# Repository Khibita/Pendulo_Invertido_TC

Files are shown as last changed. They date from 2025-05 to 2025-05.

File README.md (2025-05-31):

# 🧩 Proyecto: Péndulo Invertido

## 📋 Introducción
Este proyecto se centra en diseñar, construir y poner en marcha un péndulo invertido. Este es un sistema muy conocido en ingeniería de control porque es un ejemplo clásico de un sistema que no es lineal, es inestable y además tiene doble integración. 

El péndulo invertido presenta un desafío interesante, ya que hay que crear un sistema de control capaz de mantenerlo en equilibrio vertical desde cualquier posición inicial y frente a perturbaciones externas. Para lograrlo, se ha implementado un controlador PID usando un microcontrolador ESP32, apoyado por sensores de orientación como acelerómetro y giroscopio, y un sistema de actuadores con motores DC. 

Durante el desarrollo del proyecto, se han trabajado distintas áreas como:
- [ ] el diseño y fabricación del sistema mecánico con impresión 3D.
- [ ] la selección e integración de componentes electrónicos.
- [ ] la programación del controlador en el entorno Arduino y la sintonización del PID para validar el comportamiento del sistema.

Al final, se ha logrado crear un robot que puede mantenerse en posición vertical, resistir pequeñas perturbaciones y desplazarse controladamente. Todo el proceso está bien documentado y puedes consultarlo y reutilizarlo en este repositorio.

---

## 🎯 Objetivos
- [ ] Estabilidad en posición vertical (±5°)
- [ ] Compensación de empujones
- [ ] Arranque desde cualquier posición
- [ ] Implementación en ESP32
- [ ] Sintonización del PID

---

## 🛠️ Hardware
**Componentes usados:**
- [ ] ESP32: [WROOM 32D], elegimos está por su bajo costé, conexiones inalambricas y poder ejecutar codigo c.
- [ ] Sensor: [MPU9250], elegimos está por su bajo costé, y devolver aceleración en 9 ejes.
- [ ] Driver de motor: [TB6612FNG] se ajustaba a las caracteristicas necesarias
- [ ] Motores: [fz3176] Motor de corriente continua que se ajustaba al precio y potencia de consumo
- [ ] Batería: [ MN1604] Coloquialemente conocida de "petaca", produce 9V de alimentación, El sistema necesita más , conexión por cable, para siguie
- [ ] Regulador de Tensión: [LM7805]
- [ ] Condensador: [0.1uF y 0.2uf]
- [ ] Conectores entrada y salida :  3 de 2 pines.

-Recordar que tanto la conexión electrica , como la pcb se adjunta en este mismo repositorio.

---

## 🧱 Diseño mecánico
**Software de diseño usado:**  
- [ ] Para está pieza de geometría simple, pero que contaba con multiples caras, elegí freecad, debido que es con el estoy familiarizado por otras asignaturas y por tener entornos bien organizados y una comunidad activa. Aunque si es tu primera vez realizando este tipo de objetos con varias caras, te recomiendo aplicaciones con interfaces más modernas.

**Método de fabricación:**  
- [ ] Impresora 3D, en concreto la Anet A8. La impresión tardará bastante por culpa de los soportes, para reducir el tiempo, se podría probar o a inclinar la figura o rotar la figura para que el eje y quede como el eje x, precauición  son sujerencias no validadas. 

**Versiones del chasis y decisiones de diseño:**  
- [ ] Solo hay una versión, la publicada, en la cual prioricé que el centro de masas fuera lo más bajo posible y que estuviera centrado, apare de que no fuera necesario, tornillos más que para la placa base, aunque por como está  encastrada, no sería necesaría pasa su funcionamiento, recomiendo encarecidamente pornerlos.Para buscar un balance entre centro de masas bajo y porcentaje de ángulo de giro libre de las ruedas , sin que el chasis toque suelo, hice una incisio (diminuir el espesor a 1) en la parte baja del chasis un rectangulo para colocar la bateria , en caso de usar un portapilas más grande o una batería que superé las dimensiones de la usada habría que modificar el chasis.

---

## 🔌 Montaje
El montaje se divide en 2 partes:
- [ ] Soldar: soldar todos los componentes a la placa, en caso de querer reutilizar los componentes, recomiendo soldar conectores macho hembra a la placa en vez de los propios componentes. IMPORTANTE SEGUIR LAS DIRECCIONES DE LA PCB .
- [ ] Colocar las piezas: recomiendo empezar por la pcb una vez atornillada, seguir con los motores y por último pegar la batería con silicona al hueco posterior a la placa. 
---

## 📈 Control y software
**Controlador:** PID

**Implementación:**  
El lenguaje es .ino, compatible con  Esp32, pero las libreria en las que se basa, los pids a utilizar, está escrita en c++.

**Valores de cte del PID (Op 1 - reajustes pequeños en valores cercanos al (0,0), pero resistente a golpes fuertes):**  
- [ ] Kp = 50.0
- [ ] Ki = 1.0
- [ ] Kd = 20.0

**Valores de cte del PID (Op 1 - se mantiene quieto totalmente, pero sensible a golpes fuertes):**  
- [ ] Kp = 50.0
- [ ] Ki = 2.0
- [ ] Kd = 20.0

**PID Seleccionado**
- [ ] PID Filtrado, opción 3.

De forma resumida el codigo  compara el setpoint (posición destino) y la actual, a través del pid seleccionado, devuelve valores para los motores, que luego de ser normalizador , para enviar a los motores.

---

🎮 Control Inalambrico:

implementé la conexión por Bluetooth para que el sistema pudiera recibir órdenes en tiempo real desde un celular o una app, en mi caso serial terminal bluetooth, como si fuera un control remoto. Lo que hago es leer dos valores que llegan separados por una coma: uno controla el movimiento hacia adelante o atrás, y el otro el giro. Con esos datos, ajusto el setpoint del controlador PID para que el sistema se mueva según lo que el usuario indique, y también modifico la señal de los motores para que pueda girar fácilmente. Además, hice que el sistema mande de vuelta los valores recibidos por Bluetooth, así se puede ver desde el celular que la señal llegó bien y todo está funcionando como se espera.

---

## Resultados
**Hay que distingir dos casos según los valores de Kp, Ki, Kd elegidos:**
- [ ] Op 1:  El sistema llega conseguir estabilizarse en la mayoría de casos a golpes que incluso hagan tocar el suelo con el chasis. Una vez estabilizado empieza a tener pequeños sobre ajustes que hace que oscile un poco.
- [ ] Op 2:  El sistema consigue estabilizarse con golpes pequeños, pero en el caso de que el chasis toque suelo, no será capaz de conseguir levantarse de nuevo hasta chocar con algún objeto. Una vez estabilizado se mantiene estatico.

En resumen dependiendo de la respuestá deseada se puede elegir una u otra e incluso otras convinaciones de Kp, Ki y Kd. 

**Problemas con la Potencia**
- [ ] la conexión bluetooth hace que pierde algo de potencia los motores, por lo que es más sensible a perturbaciones, esto es debido a que el sistema no está pensado para una batería tan sencilla.
- [ ] Problemas de potencia, al romperseme los dos portapilas con que contaba tuve que hacer un arreglo con una batería de 9v auxiliar, por lo que se necesita conectar el robot a una fuente de energía. 

---

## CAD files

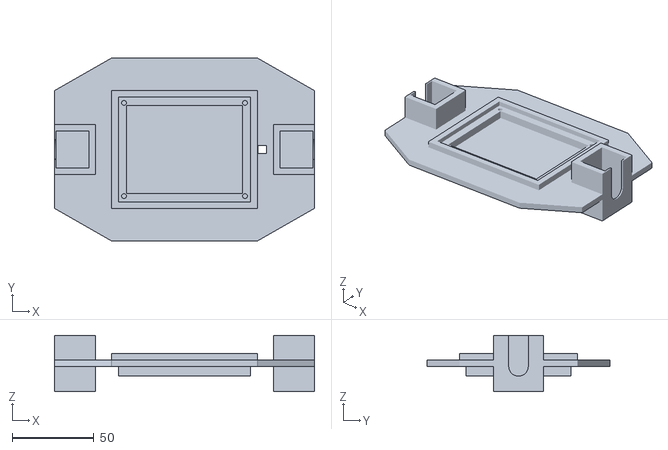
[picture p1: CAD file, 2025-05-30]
Chassis3D.stl
159.0 x 112.0 x 34.5

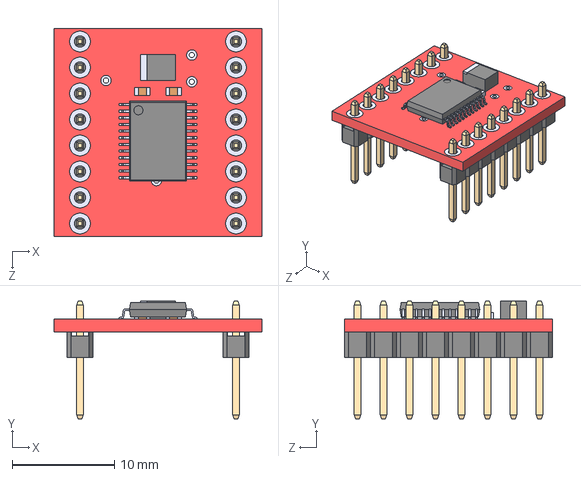
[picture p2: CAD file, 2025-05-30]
pcb-2/ROB-14450 (1)/ROB-14450.step
20.3 x 11.5 x 20.3 mm

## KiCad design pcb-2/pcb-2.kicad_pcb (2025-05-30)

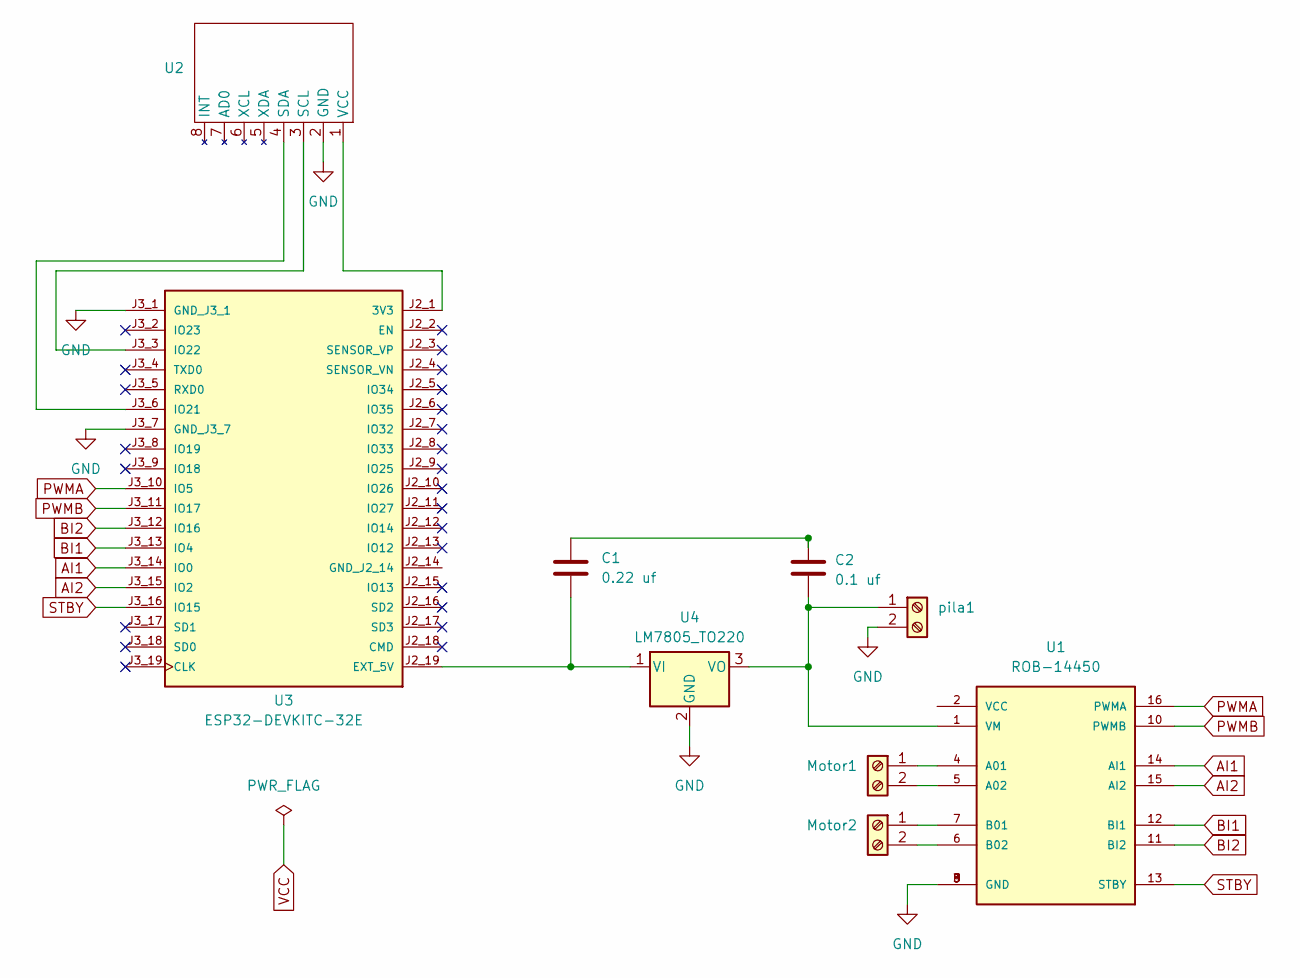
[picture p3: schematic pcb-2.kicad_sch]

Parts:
C1: 0.22 uf; CP_Radial_D5.0mm_P2.00mm
C2: 0.1 uf; CP_Radial_D5.0mm_P2.00mm
Motor1, Motor2: TerminalBlock_Phoenix_MKDS-1,5-2-5.08_1x02_P5.08mm_Horizont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
U1: ROB-14450; MODULE_ROB-14450; PARTREV 11-13-17
U2: MPU-6050
U3: ESP32-DEVKITC-32E; MODULE_ESP32-DEVKITC-32E; PARTREV 1.4
U4: LM7805_TO220; TO-220-3_Vertical
pila1: TerminalBlock_Phoenix_MKDS-1,5-2-5.08_1x02_P5.08mm_Horizont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

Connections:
AI1: U1.14 (AI1), U3.J3_14 (IO0)
AI2: U1.15 (AI2), U3.J3_15 (IO2)
BI1: U1.12 (BI1), U3.J3_13 (IO4)
BI2: U1.11 (BI2), U3.J3_12 (IO16)
GND: U1.3 (GND), U1.8 (GND), U1.9 (GND), U2.2 (GND), U3.J3_1 (GND_J3_1), U3.J3_7 (GND_J3_7), U4.2 (GND), pila1.2
unnamed: C1.1, C2.1
unnamed: Motor1.1, U1.4 (A01)
unnamed: Motor1.2, U1.5 (A02)
unnamed: Motor2.1, U1.7 (B01)
unnamed: Motor2.2, U1.6 (B02)
unnamed: C2.2, U1.1 (VM), U4.3 (VO), pila1.1
unnamed: U2.3 (SCL), U3.J3_3 (IO22)
unnamed: U2.4 (SDA), U3.J3_6 (IO21)
unnamed: U2.1 (VCC), U3.J2_1 (3V3)
unnamed: C1.2, U3.J2_19 (EXT_5V), U4.1 (VI)
PWMA: U1.16 (PWMA), U3.J3_10 (IO5)
PWMB: U1.10 (PWMB), U3.J3_11 (IO17)
STBY: U1.13 (STBY), U3.J3_16 (IO15)

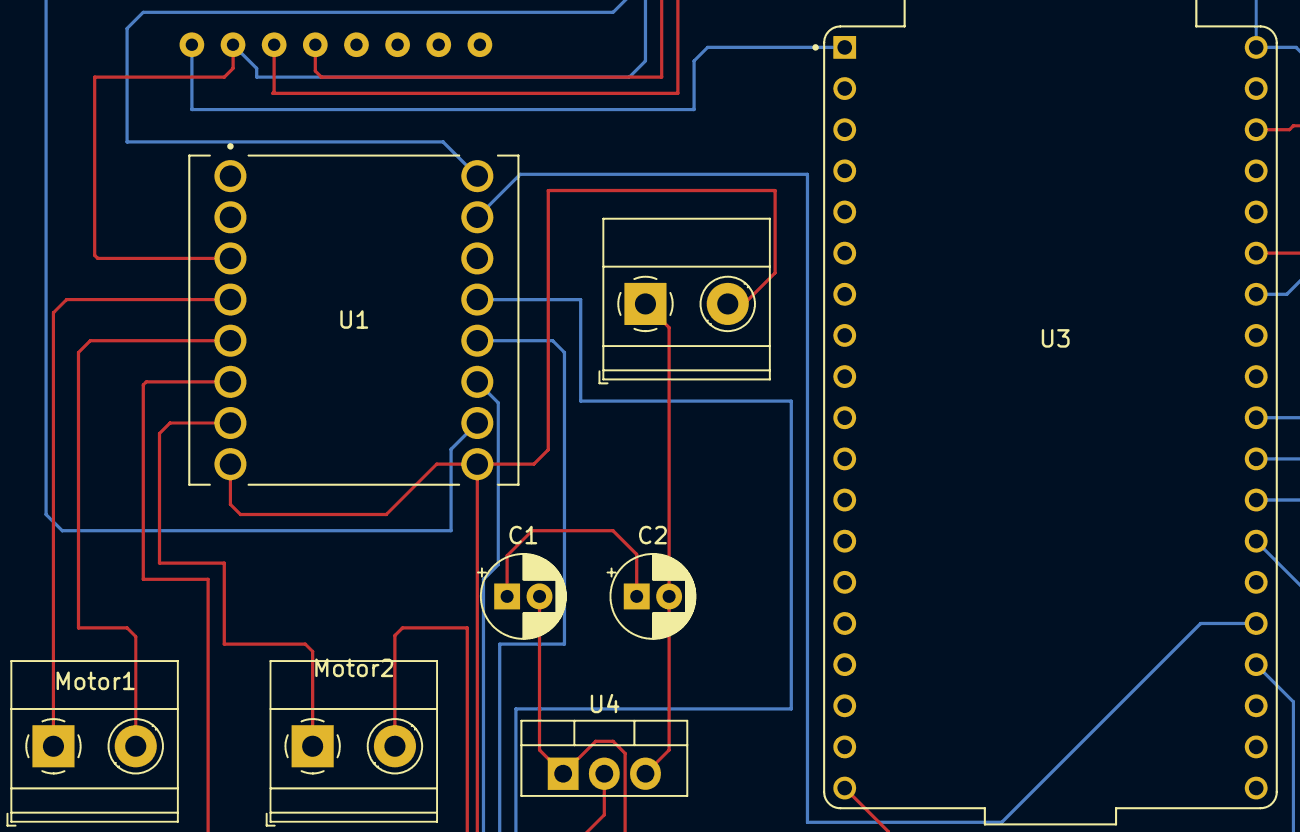
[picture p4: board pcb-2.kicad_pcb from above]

Board: 2 copper layers, 9 parts (0 on the bottom side), 18 nets.

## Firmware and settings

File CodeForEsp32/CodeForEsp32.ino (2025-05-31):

#include <Wire.h>
#include <MPU6050.h>
#include "PIDControl.h"
#include <BluetoothSerial.h>

int PID_MODE = 3; //Variable de control 
float dt = 0.005; //Periodo de actualizacion del void loop, EN SEGUNDOS
unsigned long dt_us = dt * 1e6; //Lo pasamos a microsegundos

MPU6050 mpu;
BluetoothSerial SerialBT;

const int AIN1 = 0, AIN2 = 2, PWMA = 5;
const int BIN1 = 4, BIN2 = 16, PWMB = 17;
const int STBY = 15;

//Valores, para el estado 0
float setpoint = 0.0;
float measured_value = 0.0;
float output = 0;

float desplazamientoX = 0.0;
float desplazamientoY = 0.0;

//Constantes del pid a implementar
float kp =50.0, ki = 1, kd = 20.0;

//Definimos un objeto pid, por ahora no asigmanos ninguo
PID* pid = nullptr;

void setup() {
  Serial.begin(115200);
  SerialBT.begin("ESP32Khibita");  // Nombre del dispositivo Bluetooth
  Wire.begin();
  mpu.initialize();

  //AINX y BINX pines de direccion de vel, mientras PWMX modulo de velocidad
  pinMode(AIN1, OUTPUT); pinMode(AIN2, OUTPUT); pinMode(PWMA, OUTPUT);
  pinMode(BIN1, OUTPUT); pinMode(BIN2, OUTPUT); pinMode(PWMB, OUTPUT);
  pinMode(STBY, OUTPUT); digitalWrite(STBY, HIGH);

  switch (PID_MODE) { //Elegir cual de las 3 implementacion usar
    case 1:
      pid = new PID_Discreto(kp, ki, kd, dt);
      break;
    case 2:
      pid = new PID_IIR(kp, ki, kd, dt);
      break;
    case 3:
    default:
      pid = new PID_Filtrado(kp, ki, kd, dt, 5.0);
      break;
  }
}

float getAngle() { //angulo para el plano YZ, EN GRADOS
  int16_t ax, ay, az;
  mpu.getAcceleration(&ax, &ay, &az);
  return atan2(ay, az) * 180 / PI;
}

void applyMotorA(float pwm) {
  pwm = constrain(pwm, -255, 255);
  digitalWrite(AIN1, pwm > 0 ? HIGH : LOW);
  digitalWrite(AIN2, pwm > 0 ? LOW : HIGH);
  analogWrite(PWMA, abs(pwm));
}

void applyMotorB(float pwm) {
  pwm = constrain(pwm, -255, 255);
  digitalWrite(BIN1, pwm > 0 ? HIGH : LOW);
  digitalWrite(BIN2, pwm > 0 ? LOW : HIGH);
  analogWrite(PWMB, abs(pwm));
}



void loop() {
  static unsigned long lastControl = 0;
  unsigned long now = micros(); //Devuelve los msec 
  if (now - lastControl >= dt_us) { 
    lastControl = now;

    measured_value = getAngle();
    output = pid->compute(setpoint, measured_value);
    output = constrain(output, -255, 255); // normalizar a los rangos de los motroes

    if (SerialBT.available()) { //En caso de tener Comunicacion bluethoot
      String datos = SerialBT.readStringUntil('\n');
      int sep = datos.indexOf(',');
      if (sep > 0) {
        float x = datos.substring(0, sep).toFloat();
        float y = datos.substring(sep + 1).toFloat();
        desplazamientoX = x;
        desplazamientoY = y;
        setpoint += desplazamientoY * 0.03;
      }
    }

    float pwmGiro = desplazamientoX * 2.55;
    
    //Valors para los dos motores , se resta o se suma dependiendo del sentido de giro
    applyMotorA(output - pwmGiro);
    applyMotorB(output + pwmGiro);
     
     
     
        // Enviar valores de vuelta por Bluetooth
    SerialBT.print("Recibido -> X: ");
    SerialBT.print(desplazamientoX, 2); // dos decimales
    SerialBT.print(" Y: ");
    SerialBT.println(desplazamientoY, 2);
  }
}
